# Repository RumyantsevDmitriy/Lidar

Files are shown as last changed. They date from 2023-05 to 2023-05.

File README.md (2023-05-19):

# Lidar
## Краткое описание проекта
Наш лидар предназначен для сбора точек для последующего построения 3D модели помещения. В дополнение к лидару была написана программа на С++, строящая 3D-модель по полученному облаку точек [Lidar-Viewer](https://github.com/RumyantsevDmitriy/Lidar-Viewer).
## Подробное описание
### Постановка задачи
Нашей основной задачей было создание недорогого лидара, способного сканировать не просто одну плоскость в 360 градусов, а полусферу, с большой скоростью (*P.S. ни один существующий аналог не обладает всеми этими качествами*).
### Принцип работы лидара
Моторы крутят дальномер в двух плоскостях и по прерыванию мы собираем данные с дальномера и с моторов (дистанцию до точки и углы, на которые повернулся дальномер) и записываем их в файл. Мы получаем файл с данными в сферической системе координат, открываем файл в программе [Lidar-Viewer](https://github.com/RumyantsevDmitriy/Lidar-Viewer) и либо анализируем полученную 3D-модель в этой программе, либо конвертируем файл в объектный формат в этой программе и можем открывать его в любой другой программе.
### Компонентная база лидара
- Arduino UNO – 2 шт
- Модуль датчика дальномера Benewake TFmini-S Lidar TOF – 1 шт
- Бесщеточный двигатель HT2205 – 2 шт
- Магнитный энкодер AS5048A - 2 шт
- Капсульное скользящее кольцо, 8-ми канальное, 8.5 мм в диаметре – 1 шт
- Капсульное скользящее кольцо, 18-ти канальное, 12.5 мм в диаметре – 1 шт
- Модуль Micro SD Card Reader – 1 шт
- Micro SD карта – 1 шт
- Регулятор бесколлекторного мотора – 2 шт
- Часы реального времени – 1 шт
- Аккумулятор на 12В – 1 шт
### Процесс разработки и изготовления лидара
В ходе работы было изготовлено два прототипа.
Сначала был изготовлен прототип на основе шаговых моторов.\
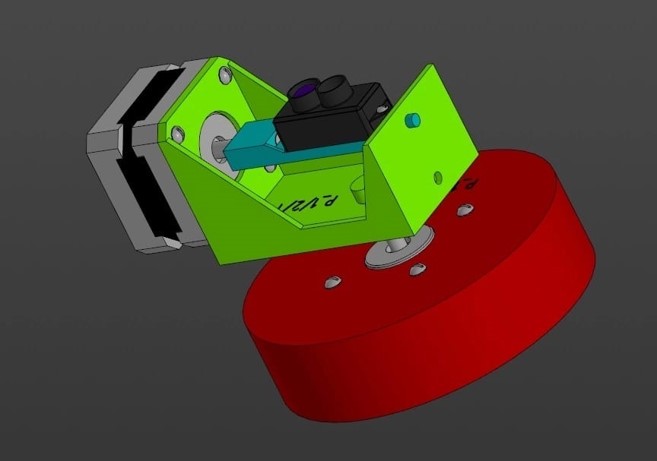
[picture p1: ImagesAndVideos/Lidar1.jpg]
Первый прототип лидара
\
В результате работы этого лидара было получено 1000 точек и достаточно хорошая 3D-модель помещения. Основным минусом этого прототипа была скорость работы, а также большая масса.\
Работа первого прототипа лидара\
В связи с этим было принято решение изготовить лидар на основе бесколлекторных моторов.\
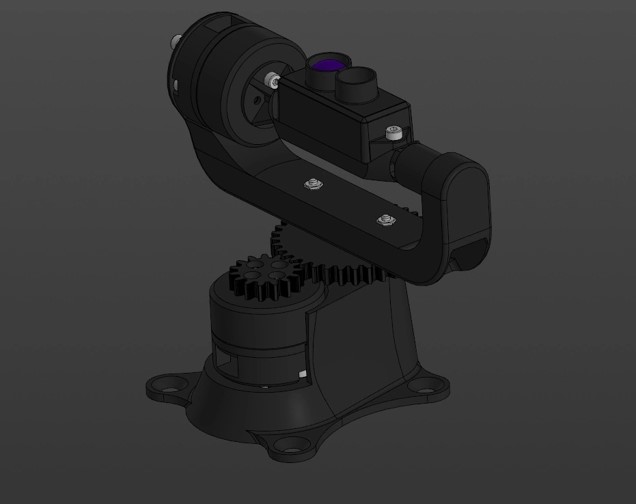
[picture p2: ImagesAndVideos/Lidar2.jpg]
Второй прототип лидара
\
В ходе разработки наша команда столкнулась с проблемой невозможности подключения дальномера и энкодеров с моторами к одной Arduino. Поэтому мы были вынуждены использовать еще одну Arduino для подключения к ней дальномера. Это привело к еще одной проблеме: теперь две независимые Arduino нужно было внешне синхронизировать для того, чтобы получать данные с разных датчиков одновременно. Для этих целей было принято решение использовать модуль часов реального времени. Общение двух Arduino между собой было реализовано с помощью hardware serial-соединения.\
Работа второго прототипа лидара\
В ходе тестирования полученного лидара была обнаружена большая проблема - нам не удавалось получать данные с дальномера и энкодеров в один момент, т.е. пока данные с дальномера доходят до Arduino, энкодеры уже посылают значения углов для другой точки. Это приводит к тому, что происходит постоянный сдвиг расстояния и углов, что в свою очередь приводит к неправильному облаку точек. Для упрощения тестирования системы мы были вынуждены переводить систему к механическому управлению: модуль часов реального времени был заменен на кнопку (и то, и то вызывает внешние прерывания системы). Тестировочный стенд лидара\
Изготовления каждого прототипа состояло из таких этапов как 3D моделирование корпусов и их печать, паяние компонентов, сборка всех компонентов воедино, написание кода, тестирование системы.\
Также была написана программа на С++, строящая 3D-модель помещения по полученному облаку точек, а также конвертирующая файл, полученный с лидара в объектный файл (.obj) - [Lidar-Viewer](https://github.com/RumyantsevDmitriy/Lidar-Viewer).\
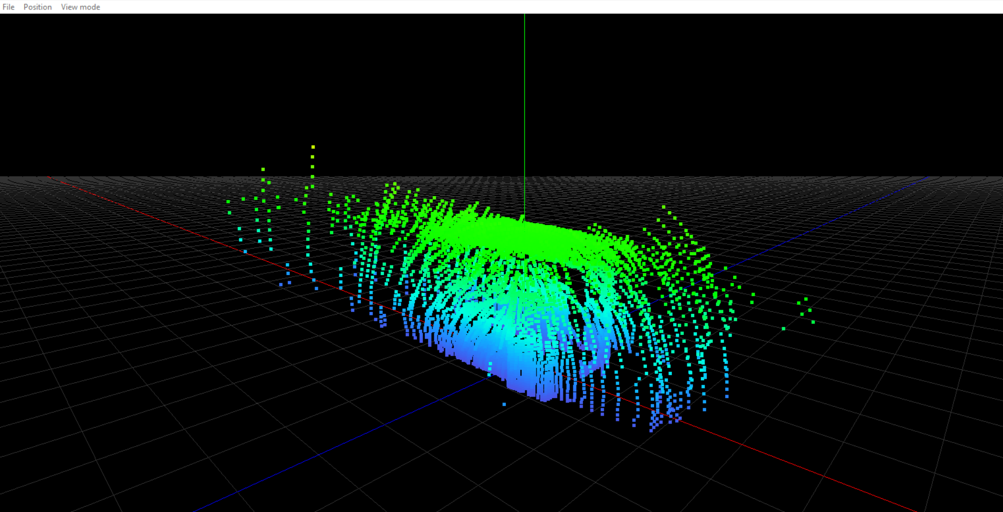
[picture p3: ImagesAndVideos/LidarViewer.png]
Работа программы

## Подведение итогов
- [X] Мы сделали два прототипа
- [X] С помощью первого прототипа получилось построить хорошую 3D-модель помещения
- [X] С помощью второго прототипа получилось собрать точки намного быстрее 
- [ ] На основе этих точек не получилось построить 3D-модель помещения
- [X] Написали программу для открытия файла с лидара и строющую эти точки
## Цели на будущее
Мы пришли к выводу, что неправильно выбрали основной микроконтроллер (Arduino UNO) и в будущем хотим перейти на микроконтроллер от STM32. Это позволит разместить все датчики на одном микроконтроллере, что приведет к упрощению схемы, ненужности внешней синхронизации, а также уменьшению задержек при передачи информации. Это позволит получать данные с датчиков синхронно, а, значит, и получить хорошую 3D-модель при помощи нашего лидара.

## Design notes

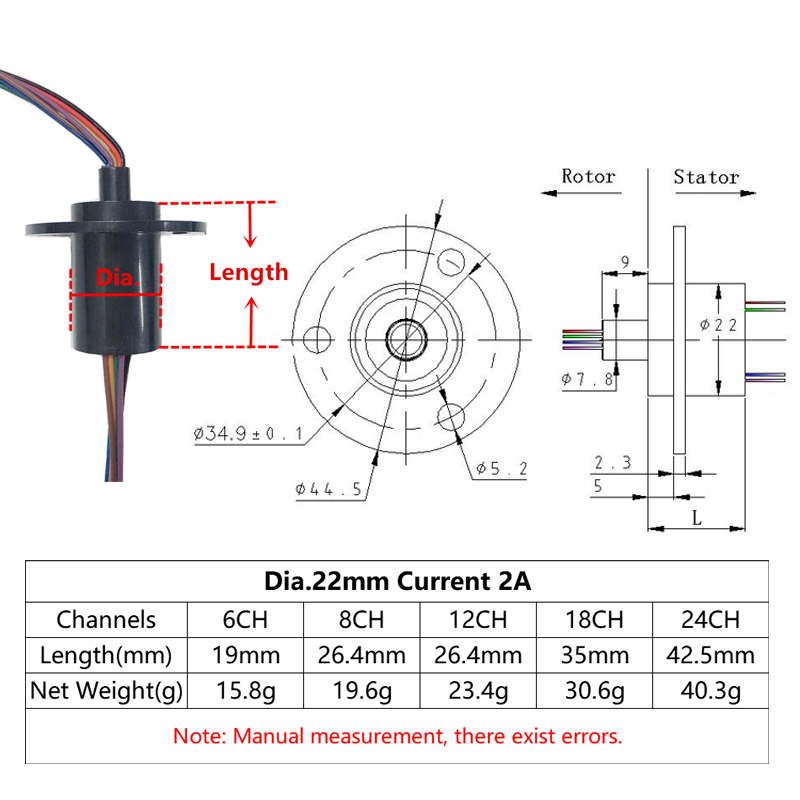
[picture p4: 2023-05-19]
LidarModels/All/Hcaac0b571b754ca28a232aaba24c2463G.jpg

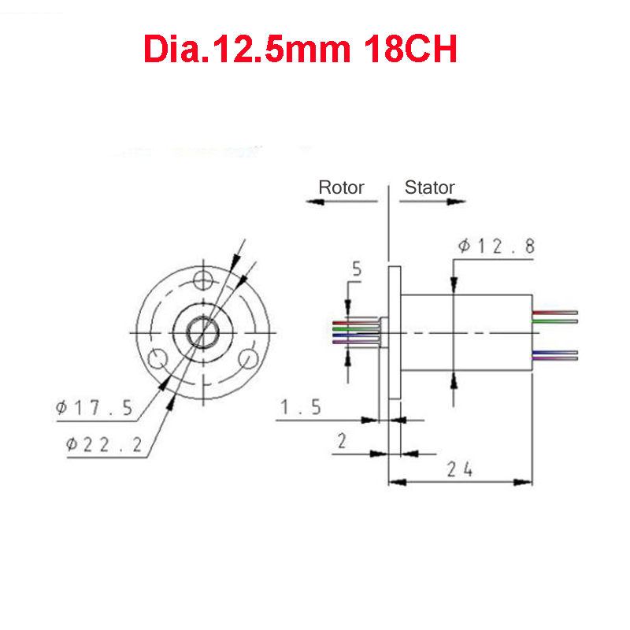
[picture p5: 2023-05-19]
LidarModels/All/Sc69ee2d4307c45c89aff494dbc3d1c7cZ.jpg

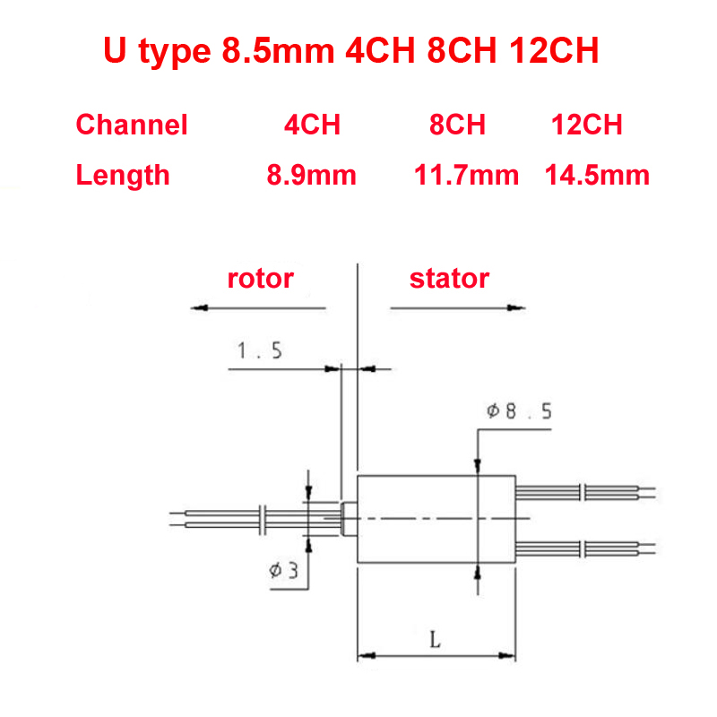
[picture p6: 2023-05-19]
LidarModels/All/S2057df0e1c9d43389dfb9e16cf5fd050j.jpg

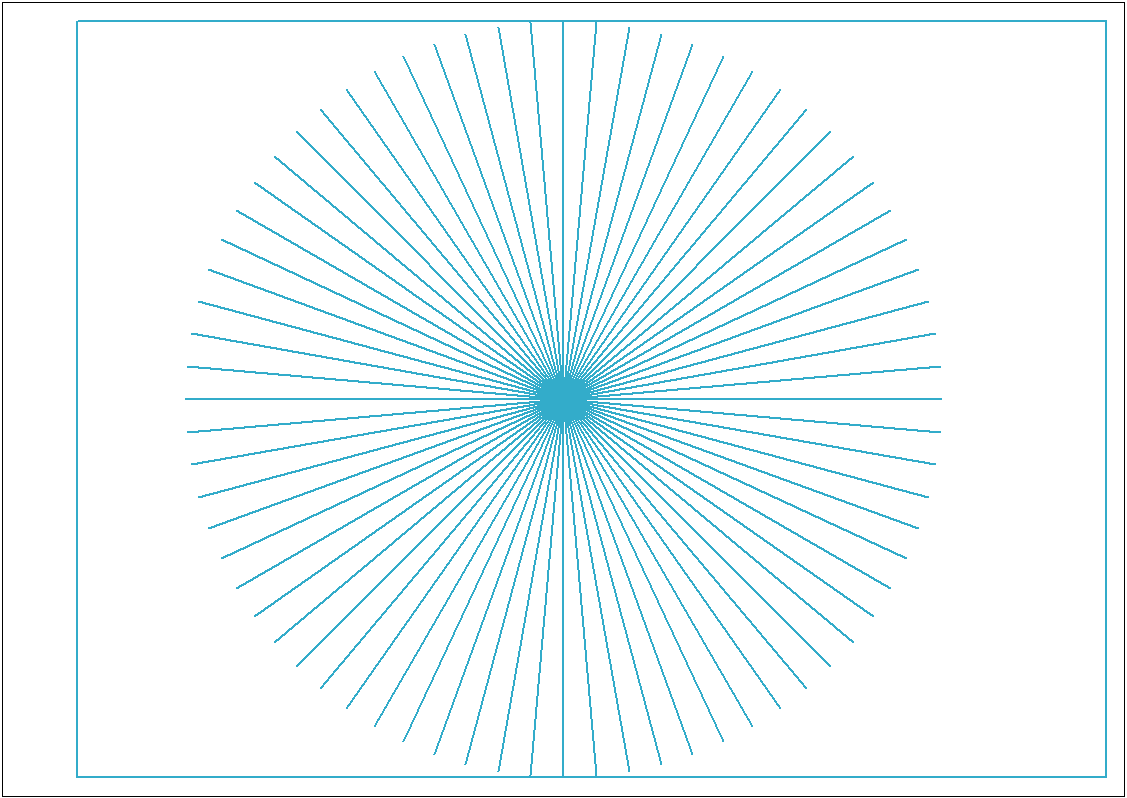
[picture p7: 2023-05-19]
LidarModels/Lidar1/STL/Чертеж.png

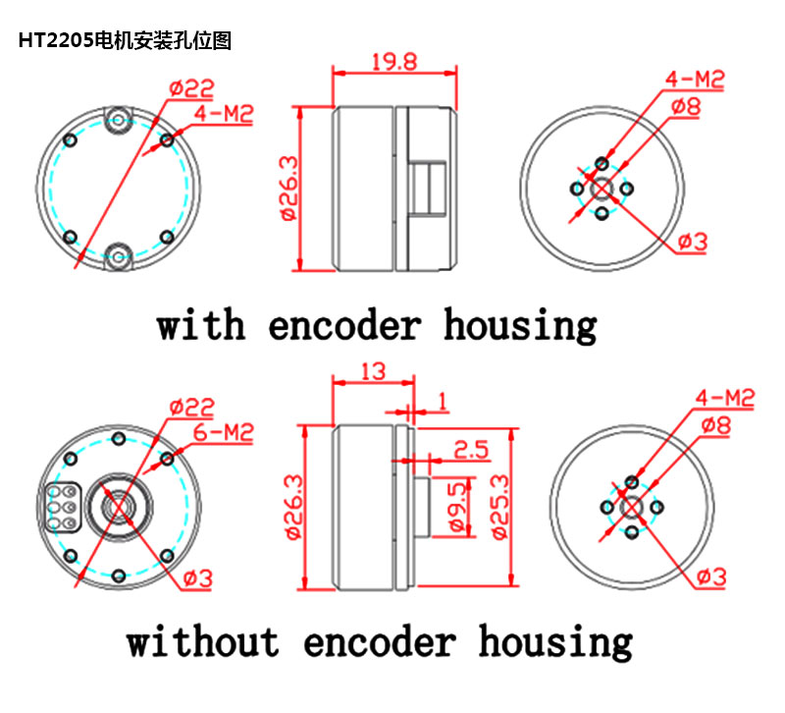
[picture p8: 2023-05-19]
LidarModels/All/Hb269df9d43a94841b1a238b253ca7962V.jpg

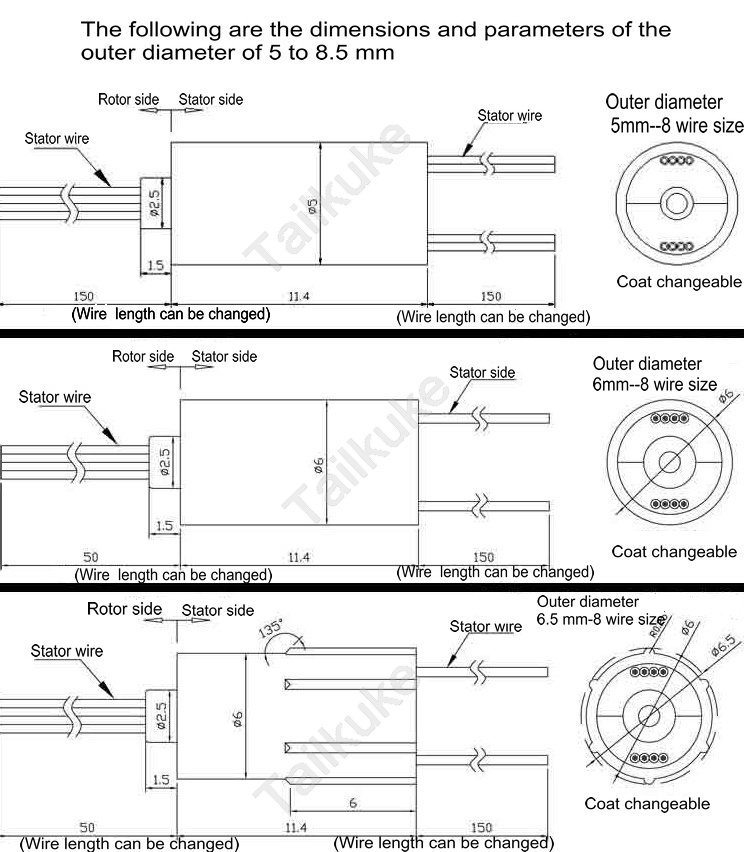
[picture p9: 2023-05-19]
LidarModels/All/Sfc979c89e0f54d589424030eccae4ee5w.jpg

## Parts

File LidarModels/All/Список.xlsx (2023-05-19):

 | название | цена | колличество | ссылка | дата доставки | цена доставки | общая цена | плюсы | минусы
LiDar | Benewake TFmini-S Lidar TOF | 3544.67 | 1 | https://aliexpress.ru/item/1005001763906831.html?sku_id=12000018808440778 | 2023-02-14 | 0 | 3544.67 | Низкая цена. Быстрая доставка. Большое колличество документации. | Небольшая дистанция сканирования (12 м). Маленькая частота (1000 Гц).
Мотор вариант 1 | JK36HM12-05041 | 1290 | 2 | https://3d-diy.ru/product/shagovyy-dvigatel-jk36hm12-05041-0-9- | 2023-02-13 | 350 | 2930 | Высокие обороты. Хорошая точность (шаг 1.8 градуса). | Огромный вес (60 г). Высокая цена.
Мотор вариант 2 | 28BYJ-48 5V | 530 | 2 | https://amperka.ru/product/stepper-motor-28byj-48-5v | 2023-02-11 | 250 | 1310 | Очень высокая точность (шаг 0.18 градуса). Умеренный вес (40 г). | Малые обороты.
 |  |  |  |  |  |  |  |  |  | цена
 |  |  |  |  |  |  |  |  |  | 7784.67

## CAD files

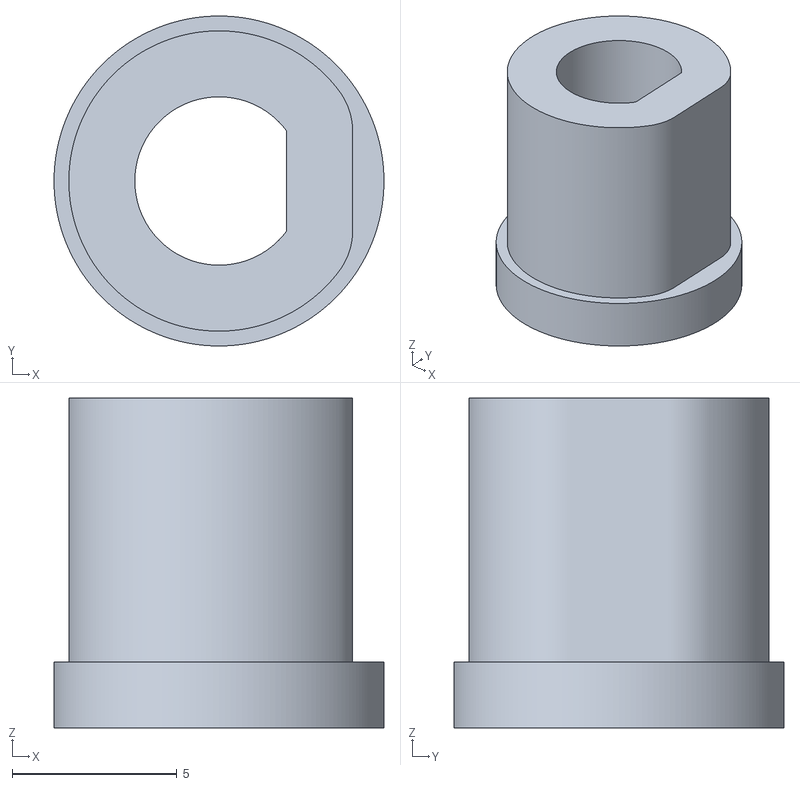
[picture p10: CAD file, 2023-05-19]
LidarModels/Lidar1/STL/пробник_0,05.stl
10.0 x 10.0 x 10.0

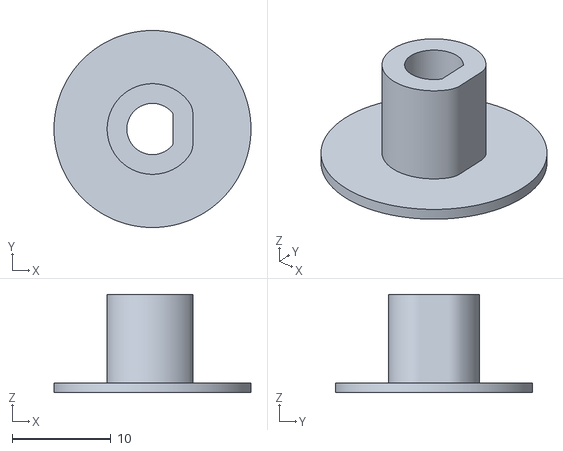
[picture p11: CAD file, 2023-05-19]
LidarModels/Lidar1/STL/пробник_0,1.stl
20.0 x 20.0 x 10.0

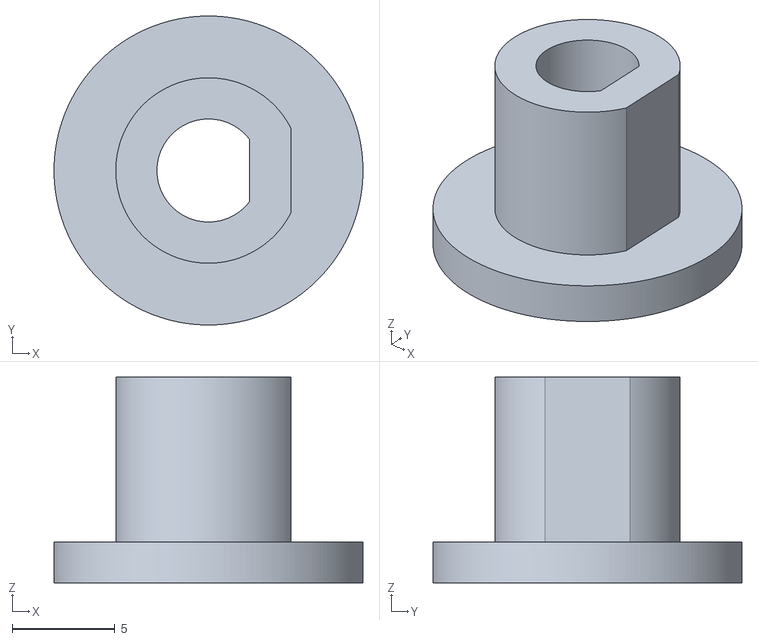
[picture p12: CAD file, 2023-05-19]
LidarModels/Lidar1/STL/пробник_0,0.stl
15.0 x 15.0 x 10.0

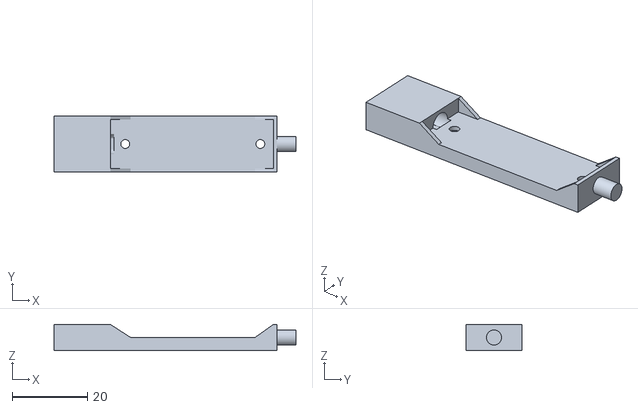
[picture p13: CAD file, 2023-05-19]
LidarModels/Lidar1/STL/Крепление_1.stl
64.5 x 15.0 x 7.00

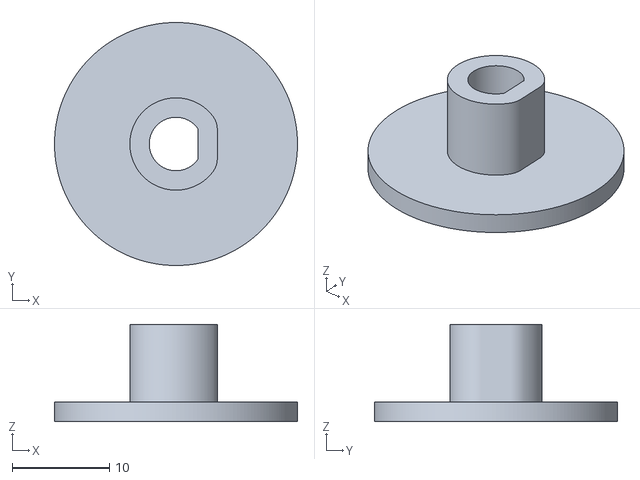
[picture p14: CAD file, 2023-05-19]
LidarModels/Lidar1/STL/пробник_0,25.stl
25.0 x 25.0 x 10.0

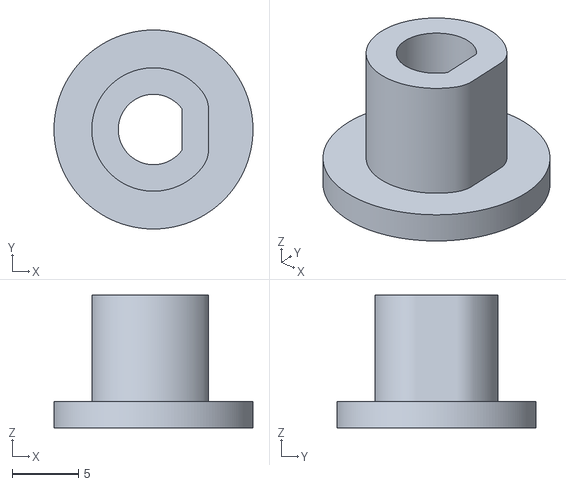
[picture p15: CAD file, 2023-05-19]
LidarModels/Lidar1/STL/пробник_0,15.stl
15.0 x 15.0 x 10.0

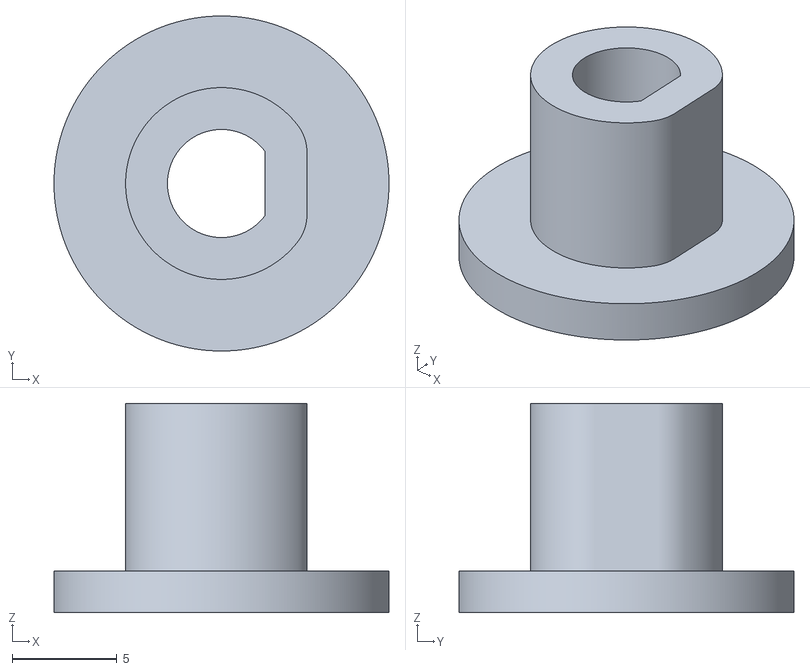
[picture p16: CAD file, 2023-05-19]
LidarModels/Lidar1/STL/пробник_0,08.stl
16.0 x 16.0 x 10.0

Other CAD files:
LidarModels/All/home2.obj

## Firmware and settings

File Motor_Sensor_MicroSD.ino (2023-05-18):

// Подключение библиотек
#include <SD.h>             // Библиотека для работы с картридером
#include <SPI.h>            // Библиотека для передачи данных по SPI
#include <Servo.h>          // Библиотека для работы с моторами
#include <SimpleFOC.h>      // Библиотека для работы с энкодерами
 
// ------------------------------------------------------------------------------------------------------------------------------------------------------------------------
// Макросы
// Определяем пины
#define PIN_MOTOR_LIDAR   5   // Пин, который подает сигнал на мотор, отвечающий за лидар
#define PIN_MOTOR_GEAR    6   // Пин, который подает сигнал на мотор, отвечающий за шестеренку
#define PIN_SENSOR_LIDAR  3   // Пин, который читает ШИМ с энкодера, отвечающего за лидар
#define PIN_SENSOR_GEAR   2   // Пин, который читает ШИМ с энкодера, отвечающего за шестеренку
#define PIN_SD            10  // Пин, который отвечает за  картридер
#define PIN_BUTTON        2   // Аналоговый пин А2, к котороу подключена кнопка

/* Модуль SD карты подключен в SPI по стандартной схеме:
  MOSI - пин 11
  MISO - пин 12
  CLK  - пин 13 */

/* Для связи со второй Arduino используется Serial соединение:
  RX -> TX
  TX -> RX 

  TX - пин 1
  RX - пин 2 */

// Остальные макросы
#define MAX_PWM 1100       // Максимальное значение ШИМ в микросекундах
#define MIN_PWM 800         // Минимальное значени ШИМ в микросекундах
#define MIN_PULSE 4         // Минимальная длина импульса в микросекундах
#define MAX_PULSE 904       // Максимальная длина импульса в микросекундах

//------------------------------------------------------------------------------------------------------------------------------------------------------------------------
// Создаем объекты                                                                         
Servo Motor_Lidar;                                                                            // Мотор, отвечающий за лидар
Servo Motor_Gear;                                                                             // Мотор, отвечающий за шестеренку              
MagneticSensorPWM Sensor_Lidar = MagneticSensorPWM(PIN_SENSOR_LIDAR, MIN_PULSE, MAX_PULSE);   // Энкодер, отвечающий за лидар
MagneticSensorPWM Sensor_Gear = MagneticSensorPWM(PIN_SENSOR_GEAR, MIN_PULSE, MAX_PULSE);     // Энкодер, отвечающий за шестеренку

// Объявляем и инициализируем переменные
float angle_Lidar, angle_Gear;
int dist;
int i = 0, n = 10;
File file;
String result;

// ------------------------------------------------------------------------------------------------------------------------------------------------------------------------
// Основное тело программы
void setup() 
{
  // Настраиваем передачу между Arduino через Serial со скоростью 115200 бод
  Serial.begin(115200);
  while (!Serial) {}

  pinMode(LED_BUILTIN, OUTPUT); 
  
  // Инициализация картридера и открытие файла для записи
  SD.begin(PIN_SD);
  SD.remove("test.txt");
  file = SD.open("test.txt", FILE_WRITE);

  // Инициализация энкодеров
  Sensor_Lidar.init();
  Sensor_Gear.init();

  // Вводим энкодеры в неблокирующий режим
  Sensor_Lidar.enableInterrupt(doPWM_Lidar);
  Sensor_Gear.enableInterrupt(doPWM_Gear);

  // Инициализация моторов
  Motor_Lidar.attach(PIN_MOTOR_LIDAR);
  Motor_Gear.attach(PIN_MOTOR_GEAR);

  // Калибровка моторов
  calibration_motor();

  // Запуск моторов
  start_motor();

  while (Serial.available() > 0) Serial.read();
  
}

void loop() 
{
  delay(2000);
  Serial.write(1);
  
  while (i < n) 
  {
    // Задаем скорость моторов
    Motor_Lidar.writeMicroseconds(1100);
    Motor_Gear.writeMicroseconds(990);

    // Обновляем энкодеры
    Sensor_Lidar.update();
    Sensor_Gear.update();

    // Прерывание при нажатии на кнопку
    if (analogRead(PIN_BUTTON) > 200) 
    {
      // Вычисляем углы
      angle_Lidar = Sensor_Lidar.getAngle();
      angle_Gear = Sensor_Gear.getAngle();

      // Считываем расстояние с другой Arduino
      while(!Serial.available()) {}
      dist = Serial.read();
      if(dist > 0)
      {
        digitalWrite(LED_BUILTIN, HIGH);
      
        result = String(dist) + " " + String(angle_Lidar * (180.0 / 3.1414)) + " " + String(angle_Gear * (15.0 / 35.0) * (180.0 / 3.1414)) + "\n";
    
        file.write(result.c_str());
        i++;
      }
      delay(200);     
    }  

    digitalWrite(LED_BUILTIN, LOW);
  } 

  // Закрываем файл для записи
  file.close();

  // Останавливаем моторы
  stop_motor();
  while(1) {}
}

//------------------------------------------------------------------------------------------------------------------------------------------------------------------------
// Функции
// Калибрровки мотора
void calibration_motor()
{
  Motor_Lidar.writeMicroseconds(MAX_PWM);
  delay(2000);
  Motor_Lidar.writeMicroseconds(MIN_PWM);
  delay(2000);
  
  Motor_Gear.writeMicroseconds(MAX_PWM);
  delay(2000);
  Motor_Gear.writeMicroseconds(MIN_PWM);
  delay(2000);
}

// Перевод энкодера, отвечающего за лидар в неблокирующий режим
void doPWM_Lidar()
{
  Sensor_Lidar.handlePWM();
}

// Перевод энкодера, отвечающего за шестеренку в неблокирующий режим
void doPWM_Gear()
{
  Sensor_Gear.handlePWM();
}

// Старт моторов (чтобы преодалеть трение)
void start_motor()
{
  Motor_Lidar.writeMicroseconds(1050);
  Motor_Gear.writeMicroseconds(1050);
  delay(1000);
}

// Остановка моторов
void stop_motor()
{
  Motor_Lidar.writeMicroseconds(0);
  Motor_Gear.writeMicroseconds(0);
  delay(1000);
}

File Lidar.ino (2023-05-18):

// Подключение библиотек
#include <TFLidar.h>        // Библиотека для работы с лидаром
#include <SoftwareSerial.h> // Библиотека для работы программного Serial

// ------------------------------------------------------------------------------------------------------------------------------------------------------------------------
// Макросы
// Определяем пины
#define PIN_TX_SERIAL 7   // Пин, к которому подключен TX-порт лидара
#define PIN_RX_SERIAL 8   // Пин, к которому подключен RX-порт лидара
#define PIN_BUTTON    2   // Аналоговый пин А2, к котороу подключена кнопка

/* Для связи со второй Arduino используется Serial соединение:
  RX -> TX
  TX -> RX 

  TX - пин 1
  RX - пин 2 */

//------------------------------------------------------------------------------------------------------------------------------------------------------------------------
// Создаем объекты                                                                         
TFLidar Lidar;                                                               // Лидар    
SoftwareSerial Serial_Lidar = SoftwareSerial(PIN_TX_SERIAL, PIN_RX_SERIAL);  // Serial-порт для связи с лидаром

// Объявляем и инициализируем переменные
int dist;

// ------------------------------------------------------------------------------------------------------------------------------------------------------------------------
// Основное тело программы
void setup() 
{
  // Настраиваем передачу между Arduino через Serial со скоростью 115200 бод
  Serial.begin(115200);
  while (!Serial) {}

  // Настраиваем общение с лидаром со скоростью 115200 бод
  Serial_Lidar.begin(115200);
  Lidar.begin(&Serial_Lidar);

  pinMode(LED_BUILTIN, OUTPUT); 
}

void loop() 
{
  
  Lidar.getData(dist);

  // Прерывание при нажатии на кнопку
  if (analogRead(PIN_BUTTON) > 200) 
  {
    digitalWrite(LED_BUILTIN, HIGH);
    Serial.write(dist);
    delay(300);  
  }
  digitalWrite(LED_BUILTIN, LOW);
}

//------------------------------------------------------------------------------------------------------------------------------------------------------------------------
// Функции
// Вычисление расстояния
int get_distance() 
{
  int dist;                     //actual distance measurements of LiDAR
  int strength;                 //signal strength of LiDAR
  int check;                    //save check value
  int i;
  int uart[9];                  //save data measured by LiDAR
  const int HEADER = 0x59;      //frame header of data package

  while (!Serial_Lidar.available()) {}

  // Check if serial port has data input
  if (Serial_Lidar.available())                
  {
    // Assess data package frame header 0x59
    if (Serial_Lidar.read() == HEADER)        
    {
      uart[0] = HEADER;
       // Assess data package frame header 0x59
      if (Serial_Lidar.read() == HEADER)     
      {
        uart[1] = HEADER;
        // Save data in array
        for (i = 2; i < 9; i++)         
        {
          uart[i] = Serial_Lidar.read();
        }
        check = uart[0] + uart[1] + uart[2] + uart[3] + uart[4] + uart[5] + uart[6] + uart[7];
        // Verify the received data as per protocol
        if (1 || uart[8] == (check & 0xff))        
        {
          // Calculate distance value
          dist = uart[2] + uart[3] * 256; 

          // Calculate signal strength value
          strength = uart[4] + uart[5] * 256; 

          while (Serial_Lidar.available()) Serial_Lidar.read();
          return dist;
        }
      }
    }
  }
}
